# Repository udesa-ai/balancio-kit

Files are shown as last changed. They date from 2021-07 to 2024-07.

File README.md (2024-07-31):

# Balancio-Kit


&nbsp;

&nbsp;



#### [README in English](README_EN.md)
----
Proyecto educativo de un robot :robot: de autobalanceo de ultra bajo costo, capaz de correr una red neuronal para mantener el equilibrio y de ser controlado de manera inalámbrica  :trackball:.

Desarrollado con fines didácticos para enseñar conceptos de RL, ML, AI y control.

<p align="center">
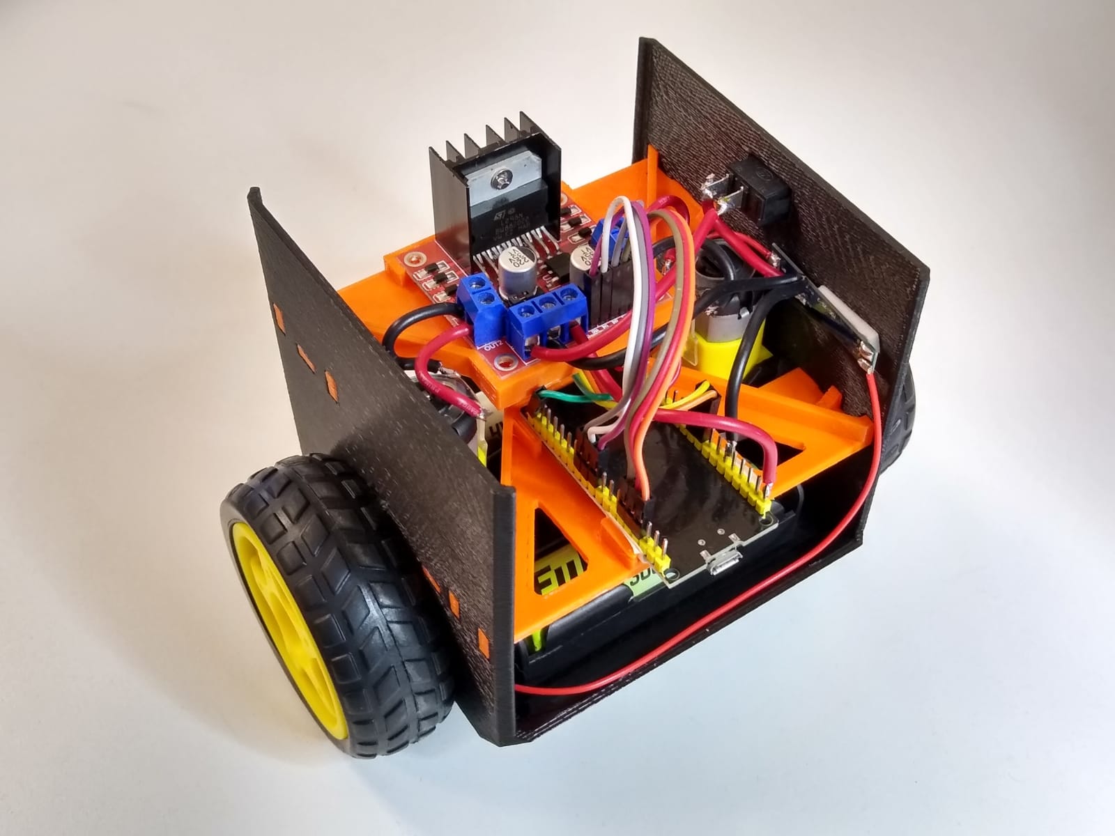
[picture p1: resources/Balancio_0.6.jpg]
    
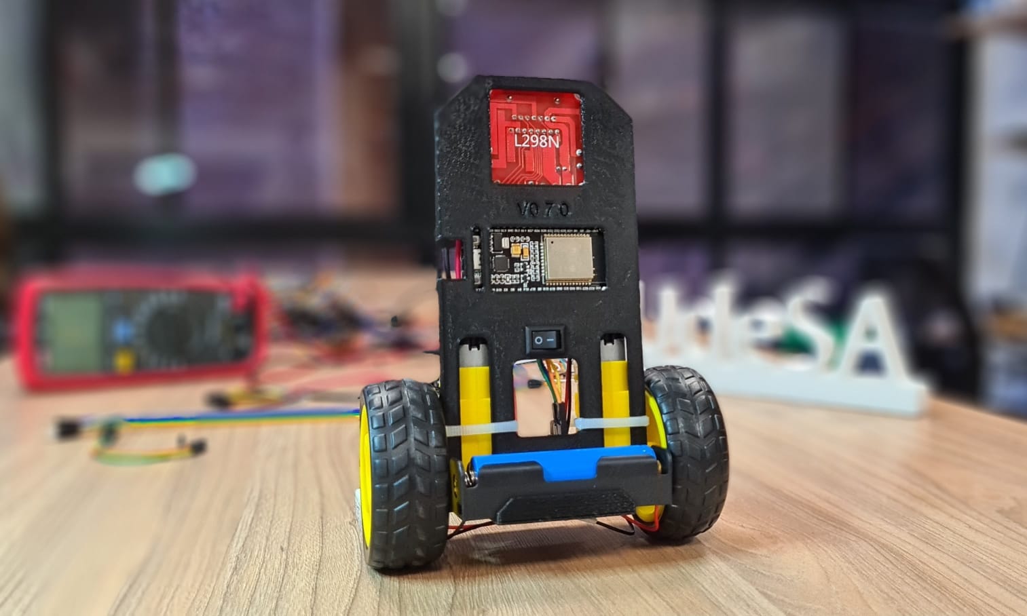
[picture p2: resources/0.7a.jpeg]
    
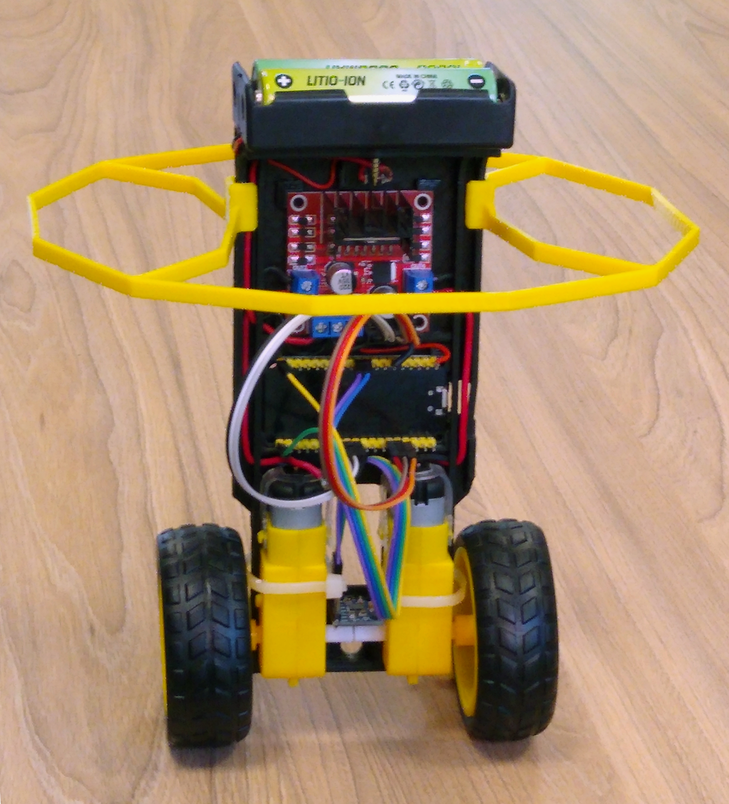
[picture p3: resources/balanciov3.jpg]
    
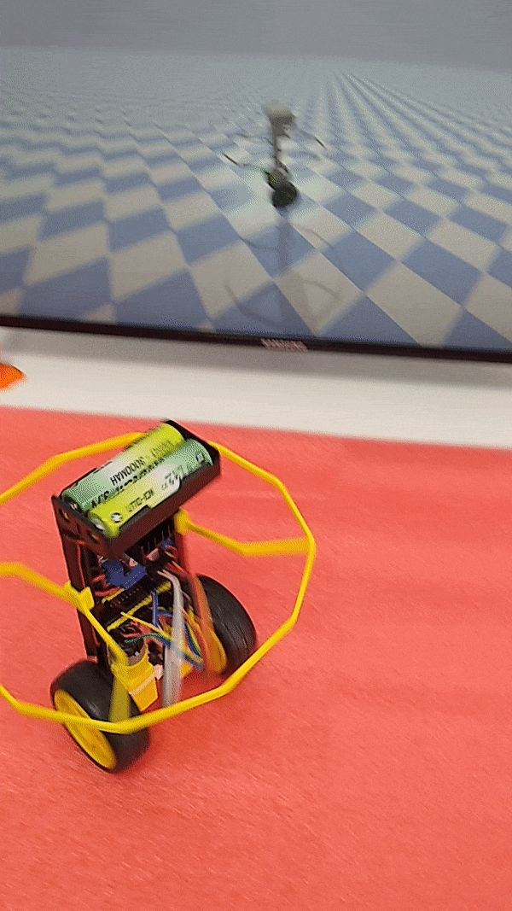
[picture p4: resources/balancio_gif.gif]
    
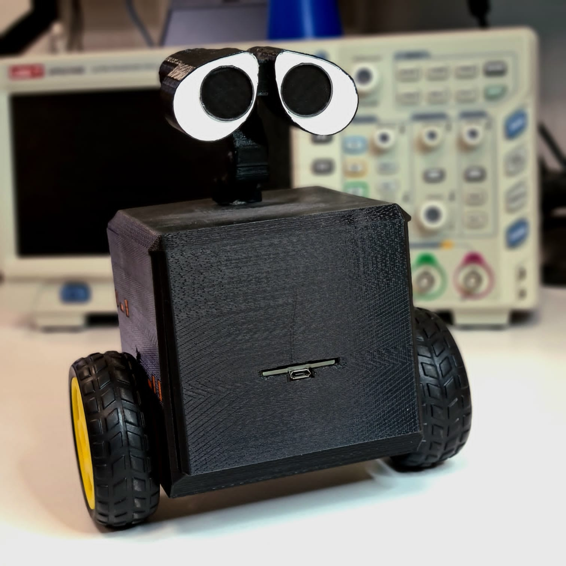
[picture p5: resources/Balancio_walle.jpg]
    
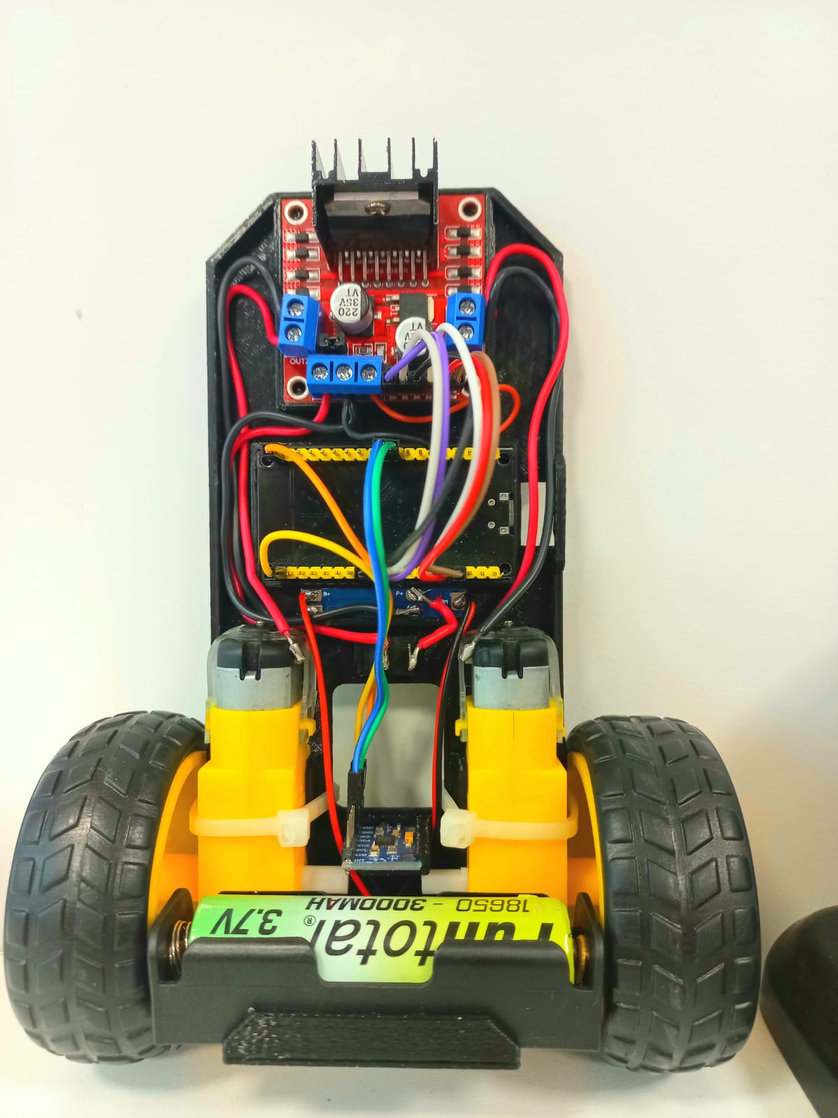
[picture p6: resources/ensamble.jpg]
    
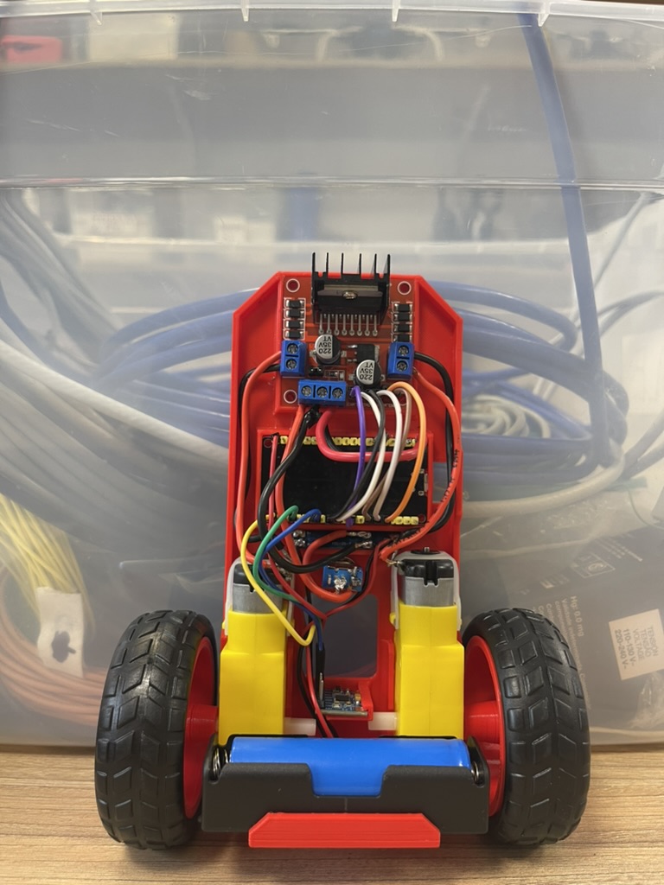
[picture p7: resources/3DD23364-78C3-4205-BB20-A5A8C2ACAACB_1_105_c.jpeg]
    
</p>

## Versiones
| | Estabilidad | Facilidad de Armado  | Requiere I3D | Tiempo de [I3D](#configuración-de-impresión)| Plano de Impresión 3D| Foto de la versión |
|:---:|:---:|:---:|---|:---:|:---:|:---:|
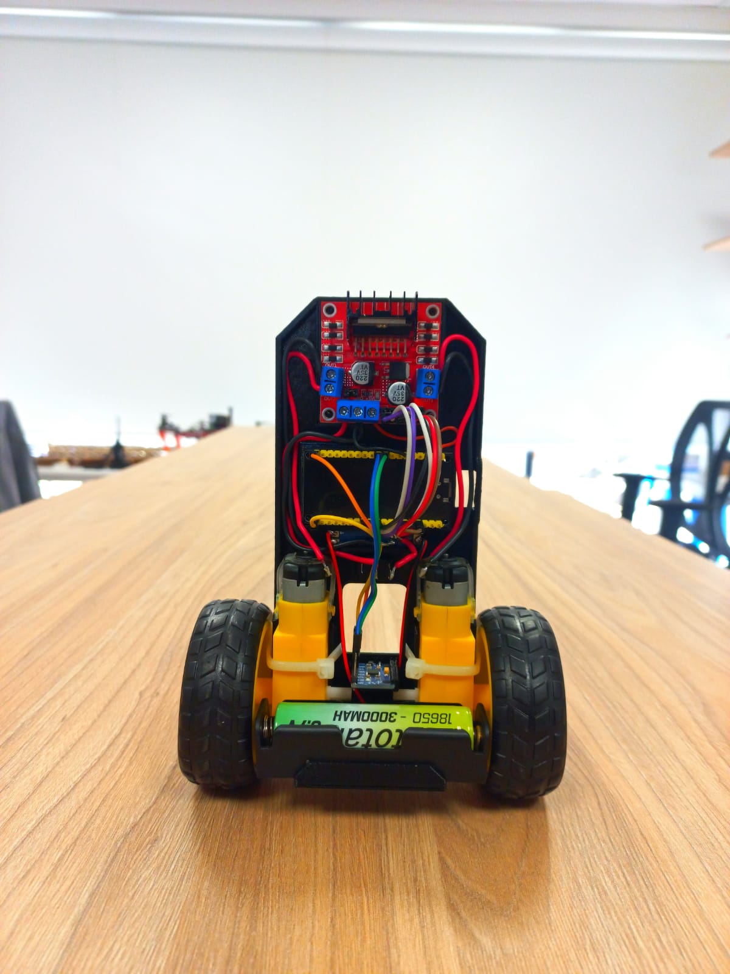
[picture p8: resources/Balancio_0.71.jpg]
| V 0.7 (Recomendado) | :star: :star: :star: | :star: :star: :star: | SI | <ul style="list-style-type:none;"> <li>  Baterias 47m </li> <li> Cuerpo 2:36 h </li> </ul> | <A HREF="https://github.com/AaronLoz/balancio-kit/tree/RL_1/Planos%20de%20Impresi%C3%B3n%203D/Version%200.7"> Versión 0.7 I3D</A> |  |
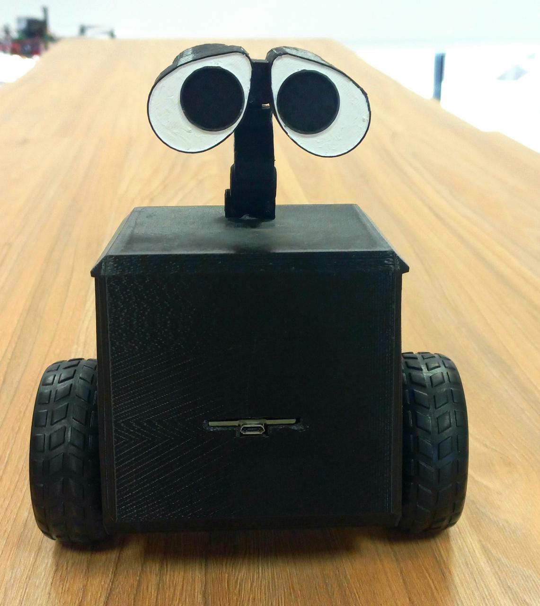
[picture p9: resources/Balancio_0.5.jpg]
| V 0.6 AKA:Wall-e | :star: :star: :star: | :star: | SI | <ul style="list-style-type:none;"> <li> C_Inferior 5:25h </li> <li> C_Superior 5:11h </li> <li>P_inferior 58m</li> <li>P_superior 55m</li> <li> Cabeza 3:19 h </li> </ul> | <A HREF="https://github.com/AaronLoz/balancio-kit/tree/RL_1/Planos%20de%20Impresi%C3%B3n%203D/Versi%C3%B3n%200.6"> Versión 0.6 I3D</A> |   |
| V 0.5 | :star: | :star: :star: :star: | SI |<ul> <li>Aro 49m </li> <li> Cuerpo 4:42h </li> | <A HREF="https://github.com/AaronLoz/balancio-kit/tree/RL_1/Planos%20de%20Impresi%C3%B3n%203D/versi%C3%B3n%200.5"> Versión 0.5 I3D</A> |  |
    
### Configuración de Impresión 
- Espesor de boquilla: 0.4 mm
- Altura de Capa: 0.3 mm 
- Perimetros: 3 
- Capas Solidas Top y Bottom:  3 
- Infill: 20%

## Componentes
| Componente | Imagen del Componente |
|:---:|:---:|
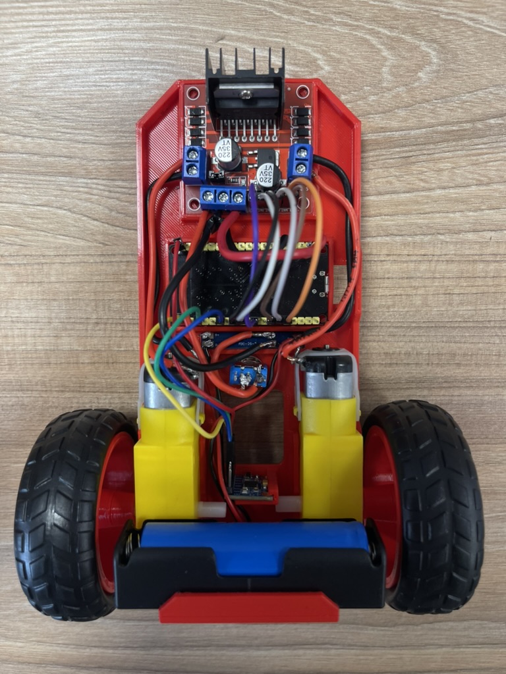
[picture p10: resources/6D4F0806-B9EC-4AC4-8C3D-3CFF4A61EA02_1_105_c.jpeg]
| Placa base (estructura en impresion 3D) |  |
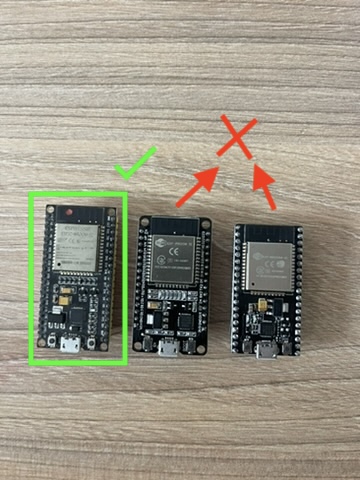
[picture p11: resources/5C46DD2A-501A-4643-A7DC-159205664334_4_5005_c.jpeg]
| Microcontrolador NodeMCU ESP32 |  |
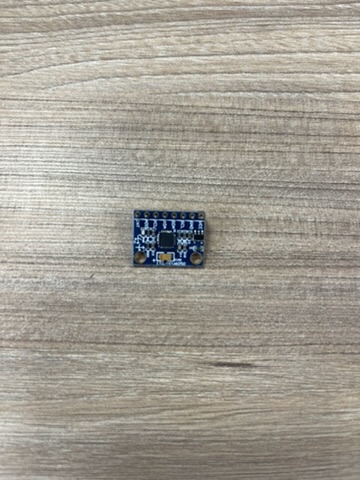
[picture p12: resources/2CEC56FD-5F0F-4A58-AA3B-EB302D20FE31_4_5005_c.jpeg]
| IMU MPU 6050 |  |
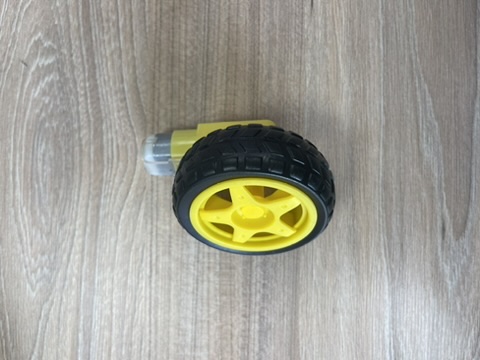
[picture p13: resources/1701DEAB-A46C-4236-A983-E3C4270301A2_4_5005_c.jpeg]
| 2 motorreductores de 6v con rueda "para Arduino" |  |
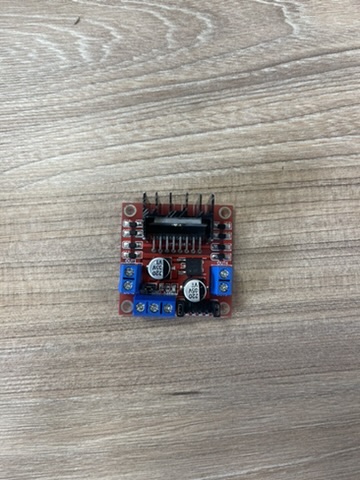
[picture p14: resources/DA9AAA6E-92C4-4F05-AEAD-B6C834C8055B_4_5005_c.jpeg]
| Puente-H L298N |  |
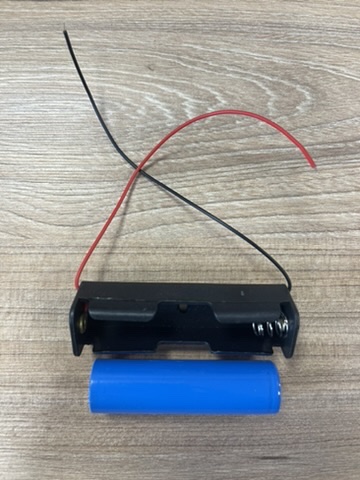
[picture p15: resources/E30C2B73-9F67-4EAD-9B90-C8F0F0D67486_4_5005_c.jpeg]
| 2 baterías 18650 con su correspondiente porta-pilas |  |
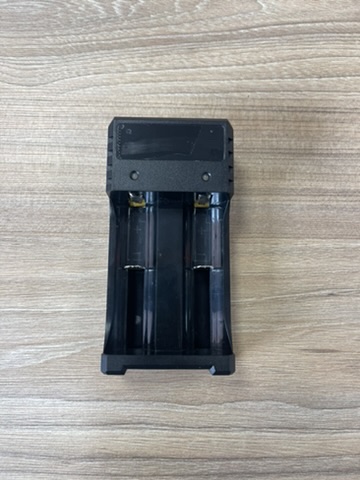
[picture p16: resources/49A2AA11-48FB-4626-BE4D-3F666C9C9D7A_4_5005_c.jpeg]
| Cargador de baterias doble |  |
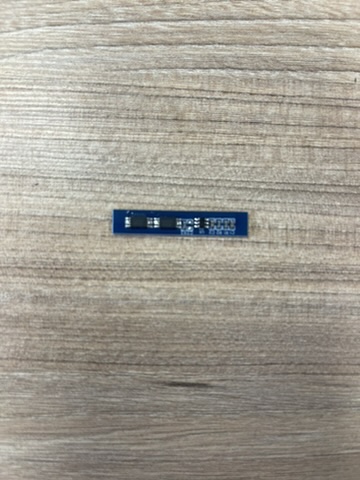
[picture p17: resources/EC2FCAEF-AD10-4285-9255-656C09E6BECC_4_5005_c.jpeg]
| BMS FCD-2S-2 |  |
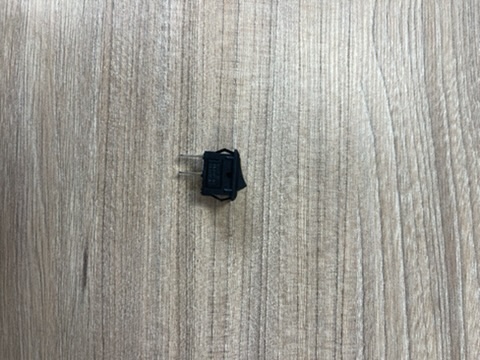
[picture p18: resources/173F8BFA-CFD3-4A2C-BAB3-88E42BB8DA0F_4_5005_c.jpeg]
| Switch |  |
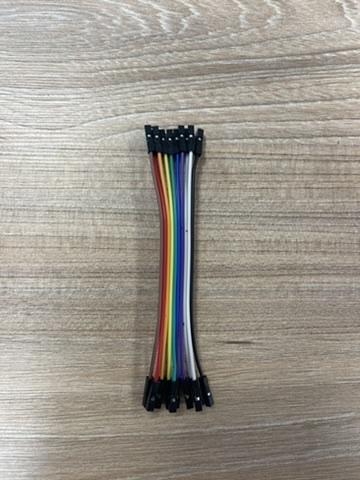
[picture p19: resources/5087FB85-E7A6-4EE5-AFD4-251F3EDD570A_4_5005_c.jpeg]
| 10 Cables DuPont |  |
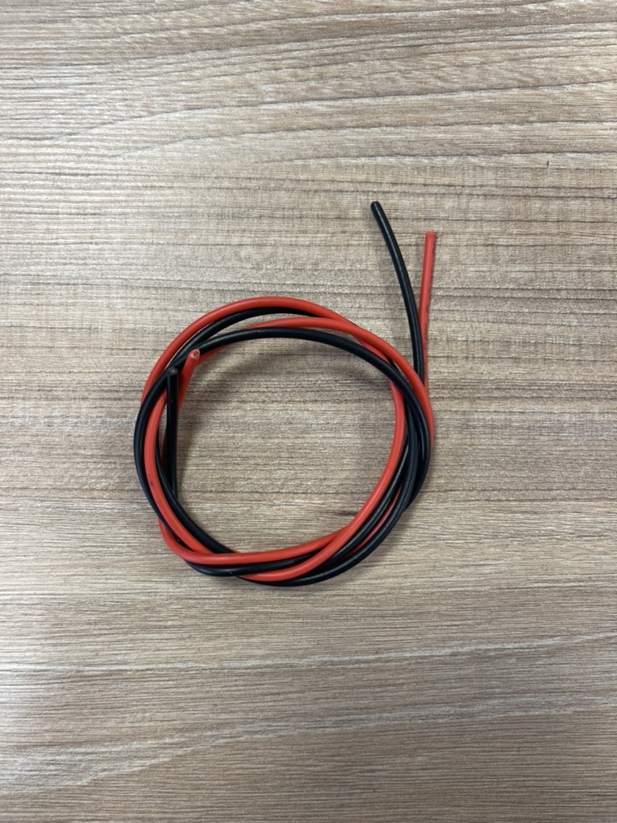
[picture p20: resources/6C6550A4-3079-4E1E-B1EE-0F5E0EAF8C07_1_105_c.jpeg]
| 1m Cable eléctrico unipolar (2x50 cm. c/u) |  |

<p align="center">
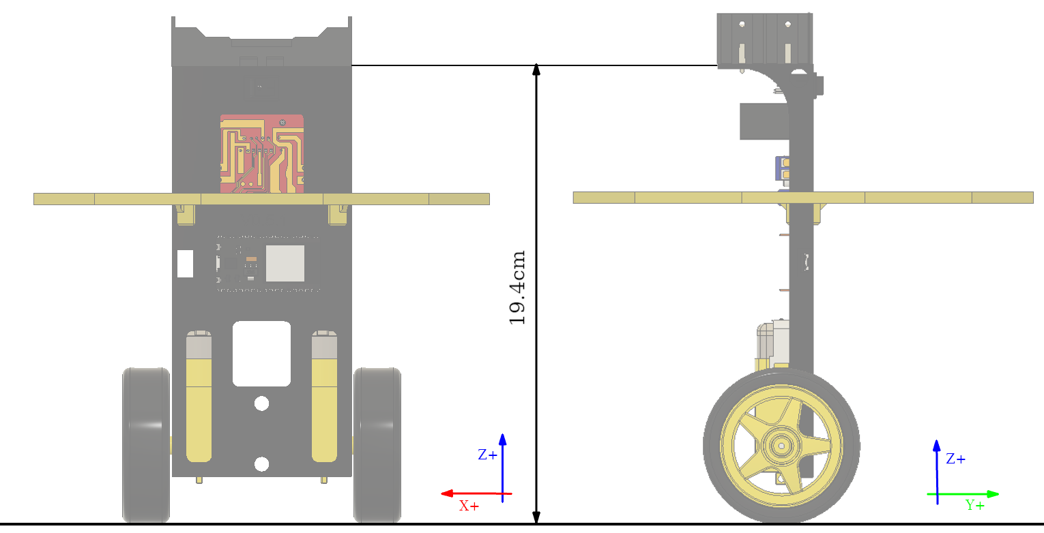
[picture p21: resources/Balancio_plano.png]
    
</p>

## Plano Electrico 
<p align="center">
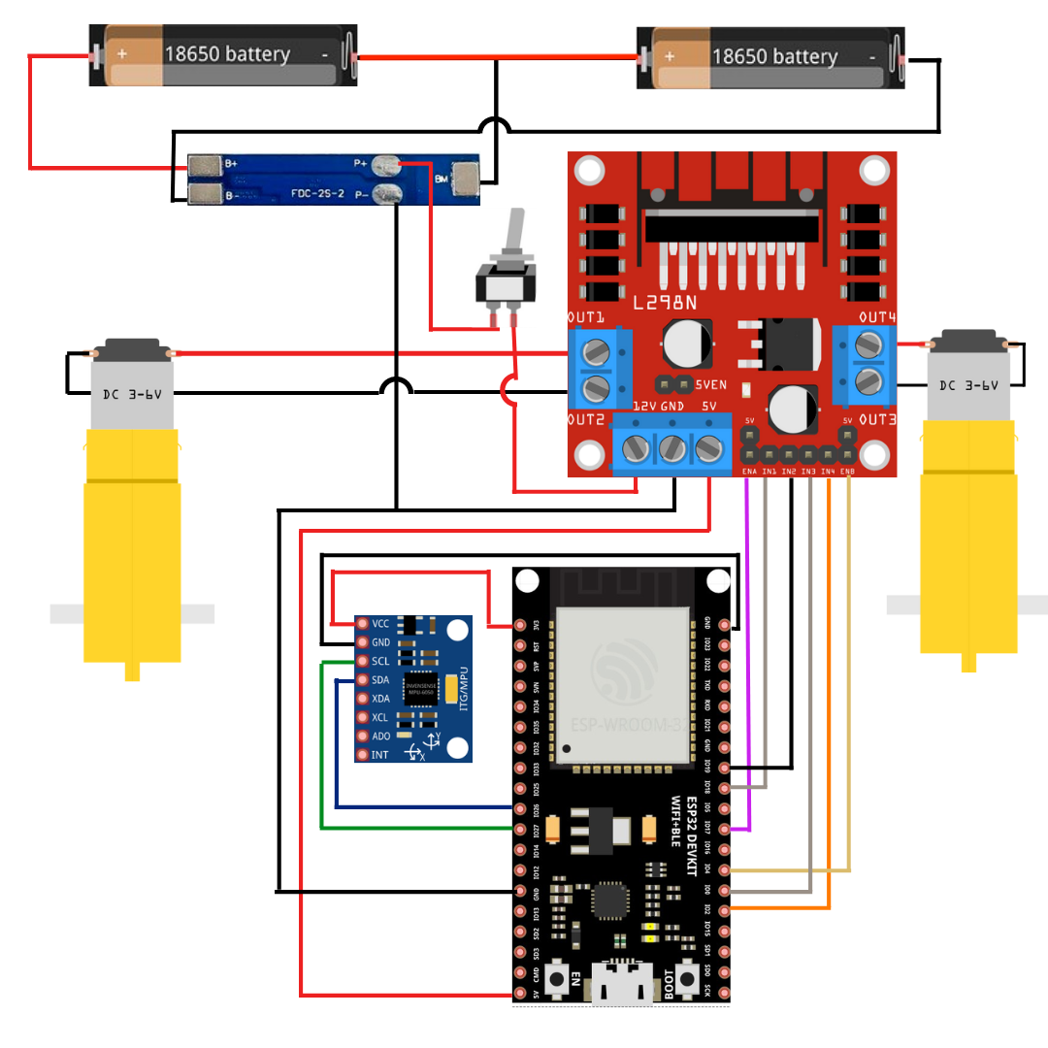
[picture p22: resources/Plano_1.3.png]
    
</p>    
    
## Ensamblaje Mecánico 
1. Imprimir en 3D alguna de las [versiones](#versiones).
1. Encastrar piezas en su posición final.
1. Sostener los motores con precintos y/o pegamento. 
1. Conectar los componentes siguiendo el [plano electrico](#plano-electrico).  
     
## Instalación :floppy_disk:

En primer lugar, se debe clonar el repositorio. Esto se puede realizar tanto descargando el mismo
como un .ZIP, o ejecutando `git clone https://github.com/UDESA-AI/balancio-kit.git` en consola.

La instalación consta de 3 módulos principales: Microcontrolador, simulación y aplicación.
Éstos son fundamentales para el funcionamiento completo del proyecto, pero la instalación
de cada uno de ellos se puede realizar en distinto orden.

### Microcontrolador

<details open>
<summary>Instalación de la IDE</summary> 
Para programar y compilar el NodeMCU ESP32 usaremos la IDE 2 de Arduino. Para esto se
debe instalar la misma siguiendo los pasos que se especifican en el siguiente 
[link](https://www.arduino.cc/en/software) .
</details> 
<details open>
<summary>Configuración del Microcrontolador</summary> 
Una vez instalada la IDE, se debe habilitar el microcontrolador que vamos a usar.
Para esto se deben seguir los siguientes pasos:
    
1. En la IDE, ir a 'File' (Archivos) → 'Preferences' (Preferencias)
    
2. En el campo "Additional Boards Manager URLs", agregar lo siguiente: https://dl.espressif.com/dl/package_esp32_index.json. (Luego clickear 'OK').
3. Ir a 'Tools' → 'Board: ' → 'Boards Manager…' 
    
4. Buscar "esp32", e instalar "esp32 by Espressif Systems" (version 2.x) presionando el botón 'Install'.
    
5. Indicarle a la IDE que vamos a utilizar un esp32. Ir a 'Tools' → 'Board:' → 'ESP32 Arduino' → 'NodeMCU-32S'
    
6. En 'Tools' → 'Port', seleccionar el puerto correspondiente a donde está conectado el microcontrolador.

</details> 

<details open>
<summary>Librerias de Arduino</summary> 
Luego procederemos a instalar las librerías de arduino que vamos a utilizar:

- Para eso ir a 'Sketch' → 'Include Library' → 'Manage Libraries…'

- Buscar e instalar las siguientes librerias, especificando la versión correspondiente:
    - MPU6050 by Electronic Cats (version 1.0.0)
    - PS3 Controller Host by Jeffrey van Pernis (version 1.1.0)
    - EloquentTinyML by Simone Salerno (version 0.0.7)

</details> 
<details open>
<summary>Ejecución inicial</summary> 
Para comprobar la instalación, ejecutaremos un ejemplo de prueba:
- ir a 'File' → 'Examples' → 'WiFi' → 'WiFiScan'
- En el sketch generado, presionar el botón de carga ('Upload')  :calling:
- Si todo funcionó correctamente, debe aparecer un mensaje 'Done uploading' en la consola.

Posibles errores:
- Si no se puede cargar el programa al microcontrolador, intentar mantener presionado el botón "boot" presente en la placa, mientras se realiza la carga. Esto se debería realizar solo la primera vez.
</details> 

### Simulación
La simulación es opcional, no es necesaria para el funcionamiento y armado del robot. Se puede pasar directamente a la parte de calibración.
<details open>
 
La simulación corre en Python :snake:, y utiliza diversos paquetes. Para facilitar la instalación de los mismos, utilizaremos [Conda](https://docs.conda.io/en/latest/).

Se debe seguir con los siguientes pasos:

1. Para el uso e instalación de conda, descargaremos miniconda (también se puede instalar [Anaconda](https://docs.anaconda.com/anaconda/install/index.html)), siguiendo con los pasos que se especifican en el siguiente [link](https://docs.conda.io/en/latest/miniconda.html#installing).
2. Crearemos un 'Environment' de conda, donde alojaremos nuestros paquetes. 
   Esto se puede realizar tanto desde la consola (en el caso de haber descargado Miniconda) o desde una GUI (en caso de haber descargado Anaconda). Respectivamente:
    - Miniconda: Ejecutar el siguiente comando en la consola: `conda env create -f requirements.yml`. Donde `requierments.yml` es el [archivo](https://github.com/UDESA-AI/balancio-kit/blob/RL_1/requirements.yml) que se encuentra dentro del repositorio y ya fue descargado.
    - Anaconda: En la GUI de Anaconda: En la pestaña environments, hacer clik en import y especificar [archivo](https://github.com/UDESA-AI/balancio-kit/blob/RL_1/requirements.yml) en file

<p align="center">
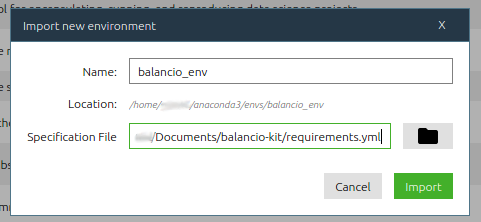
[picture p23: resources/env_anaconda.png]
    
</p>

3. Activar el environment creado, llamado **balancio**:
    - Miniconda: Ejecutar en terminal `conda activate balancio`
    - Anaconda: En la pestaña environments, hacer clik en el ambiente que se quiere activar
4. Dentro del environment activado, ejecutar el archivo [setup.py](https://github.com/UDESA-AI/balancio-kit/blob/RL_1/simulation/balancio_lib/setup.py):
    `python setup.py`
5. Probar la instalación, corriendo el siguiente [script](https://github.com/UDESA-AI/balancio-kit/blob/RL_1/simulation/pid.py):
    `python pid.py`
    </details> 

### Variables Físicas de la versión 0.7
#### Cuerpo
Masa sin ruedas: 0.244 kg

Posición del centro de masa con respecto al eje de los motores y el centro simétrico del cuerpo: 

- x = 1.55 
- y ~= 0 mm
- z = 31 mm

Inercia sin ruedas desde el centro de masa (kg.m2): 

- Ixx = 0.0006945
- Ixy ~= 0
- Iyy = 0.0006536
- Ixz = -0.000013447 
- Iyz ~= 0
- Izz = 0.0001937

#### Rueda
Masa de una rueda: 0.029 kg

Posición del centro de masa con respecto al eje de los motores y el borde del agarre: 
- x = 0 mm   
- y = 15.6 mm 
- z = 0 mm

Inercia de la rueda desde el centro de masa (kg.m2):  

- Ixx = 0.000011729 
- Ixy ~= 0  
- Iyy = 0.000021531 
- Ixz ~= 0 
- Iyz ~= 0 
- Izz = 0.000011729

### Aplicación 

 La aplicación está creada en <A HREF="https://appinventor.mit.edu/"> MIT App Inventor </A>.

Simplemente entrar al website e importar el .aia en <A HREF="Balancio-kit/app/app.aia"> App Balancio  </A>. Luego de esto, se puede usar la aplicación mediante bluethooth desde un celular.

## Calibración

Estas instrucciones asumen conocimiento del uso de la IDE arduino

<details open>
<summary>Calibración del IMU</summary>
1. Abrir `Balancio-kit/Mcu/Src/imu_calibration/imu_calibration.ino` con el IDE Arduino
    
2. Colocar el robot con la IMU paralela al piso y mantenerlo firme

3. Subir el programa a la placa y usar el monitor serial para obtener las compensaciones de la IMU

4. Modificar las compensaciones de giróscopo en el archivo `balancio-kit/mcu/src/main/config.h` en:
```c++
// IMU calibration parameters
#define X_ACCEL_OFFSET -1775
#define Y_ACCEL_OFFSET  756
#define Z_ACCEL_OFFSET  2706
#define X_GYRO_OFFSET   181
#define Y_GYRO_OFFSET   77
#define Z_GYRO_OFFSET   60
```
5. Para las compensaciones de Acelerómetro debe ser tenido en cuenta la gravedad, solo midiendo las compensaciones con la gravedad perpendicualar a esa direcci 
</details>  

<details open>
<summary>Calibración del angulo de equilibrio</summary>
1. Abrir `balancio-kit/mcu/src/main/main.ino`

2. Sostener el robot en la posición de equilibrio

3. Subir el programa a la placa y usar el monitor serial para obtener las compensaciones de angulo

4. Modificar en angulo de equilibrio en el archivo `balancio-kit/mcu/src/main/config.h` en la línea:
```c++
// Angle of (approximate) static equilibrium
#define STATIC_ANGLE -0.04 // Calibrated point
```
 </details>   
 
<details open>
<summary>Calibración de las constantes PID</summary>
    
1. Sacar el jumper de 12v en el driver 

2. Elegir parámetros PID
    
3. modificar las constantes del PID en el archivo `balancio-kit/mcu/src/main/config.h` en las líneas:
```c++
// PID Constants for pitch control
#define KP 2000
#define KI 22000
#define KD 20.0
```   

4. Probar las constantes, si se sacó el jumper se puede probar incluso con el cable conectado. **Cuidado al hacer esto!**

---
</details> 
     
Una vez configurado correctamente el robot, se pueden seleccionar distintos parametros de configuracion en el archivo correspondiente (`config.h`). 

Entre ellos, se puede seleccionar el tipo de controlador deseado para estabilizar el Balancio.

Por ejemplo, en caso de querer utilizar un controlador PID:
```c++
// Control algorithm type
#define CONTROL_ALGO "PID"
```

En caso de querer utilzar un agente de aprendizaje por refuerzo:
```c++
// Control algorithm type
#define CONTROL_ALGO "RL"
```
</details> 

---
## TODO

- [x] initial commit
- [x] Desarrollar aplicación bluetooth
- [x] Crear agente RL
- [x] Diseño mecánico
- [X] Publicar STL del diseño mecánico
- [ ] Publicar STEP del diseño mecánico
- [X] Crear diagrama electrónico
- [ ] Aclarar que datos levantar del imu calibration.

## Bugs conocidos
- [x] Wheel spins on startup

## Contribuciones
 
Las *pull requests* son bienvenidas, para cambios mayores, por favor abrir un *issue* para discutir los cambios deseados

## Licencia
[MIT](https://choosealicense.com/licenses/mit/)

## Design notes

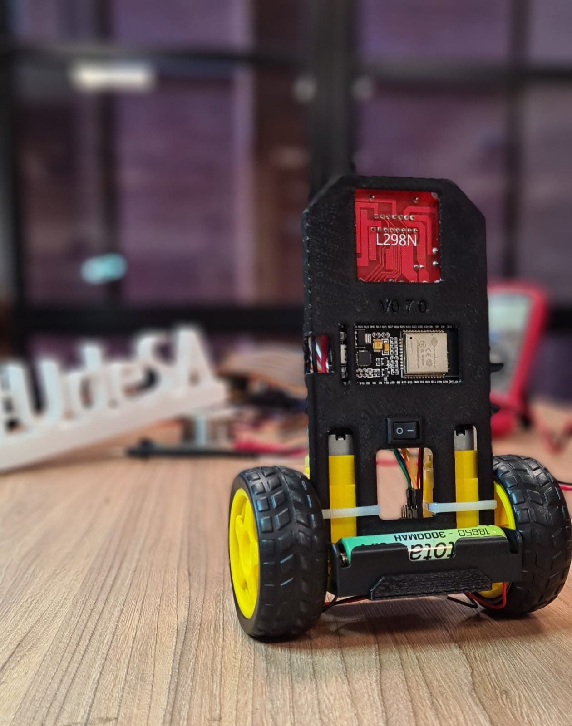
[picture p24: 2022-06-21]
resources/0.7b.jpeg

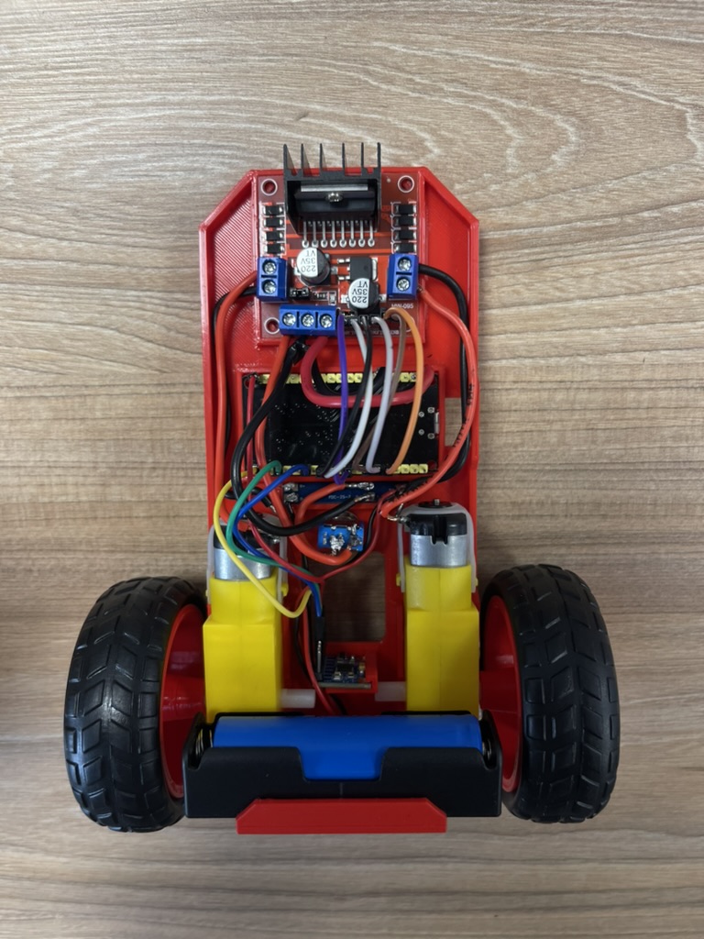
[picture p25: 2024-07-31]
resources/710C4956-F81B-4884-B3D5-5948F854DA13_1_105_c.jpeg

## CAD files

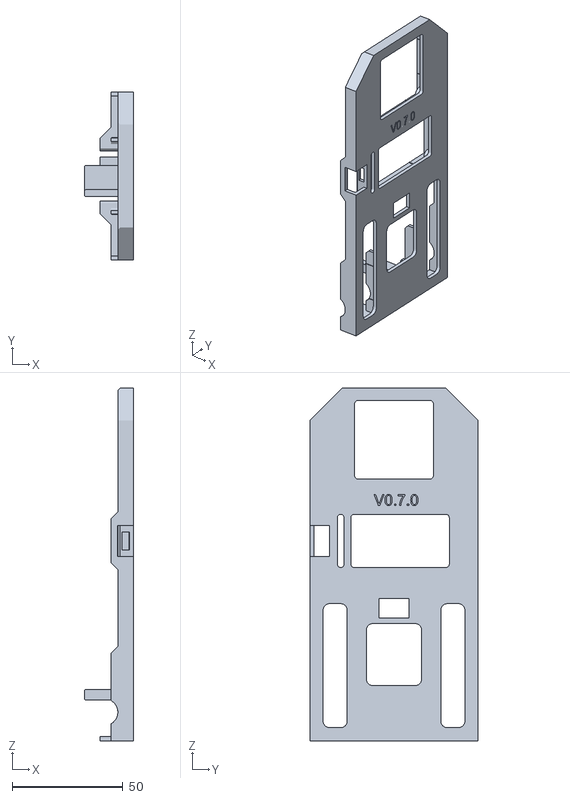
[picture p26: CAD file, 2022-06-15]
Planos de Impresión 3D/Version 0.7/Body_v0.7.stl
22.0 x 76.0 x 159.3

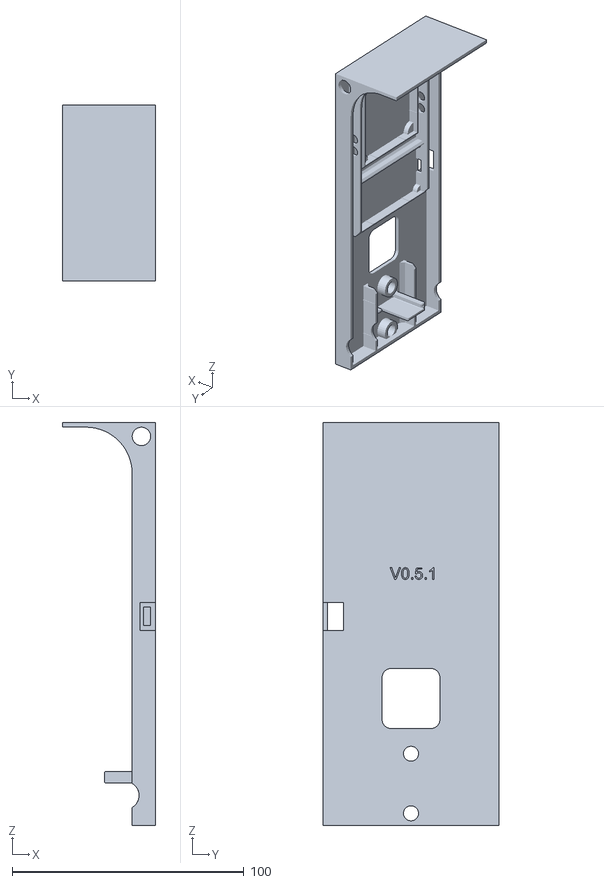
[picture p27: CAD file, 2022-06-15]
Planos de Impresión 3D/versión 0.5/Cuerpo.stl
40.0 x 76.0 x 174.0

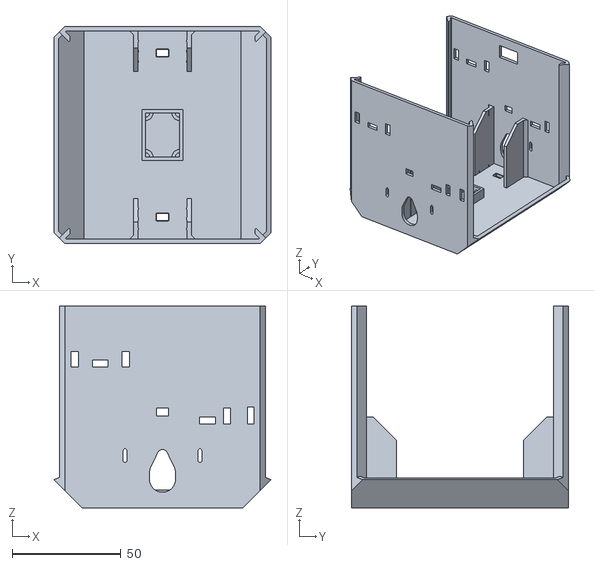
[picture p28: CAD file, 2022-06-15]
Planos de Impresión 3D/Versión 0.6/Cuerpo_Inferior.stl
100.0 x 100.0 x 93.0

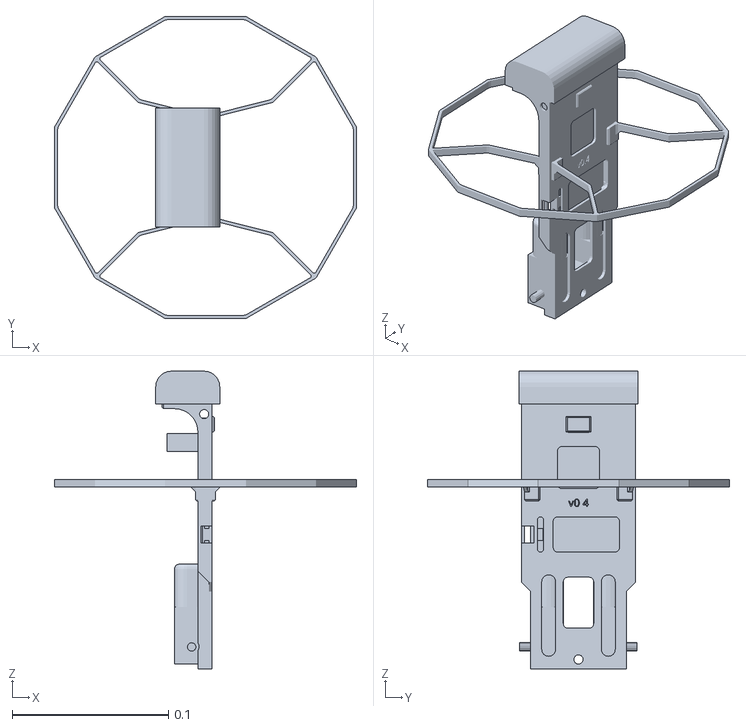
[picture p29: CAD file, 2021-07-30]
simulation/stl/Body.stl
0.193 x 0.193 x 0.19

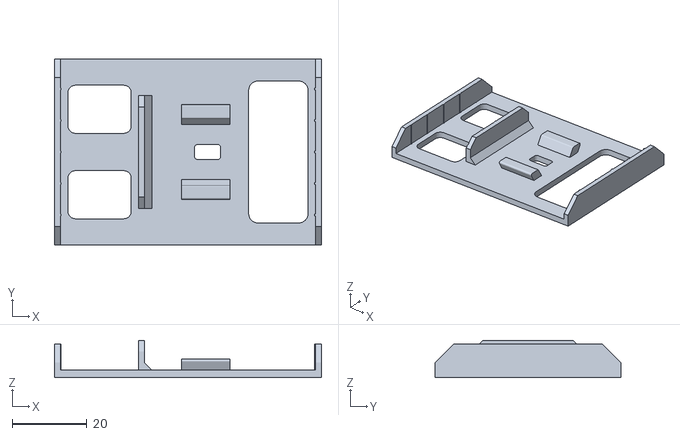
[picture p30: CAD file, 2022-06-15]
Planos de Impresión 3D/Version 0.7/Battery_Holder_Holder.stl
71.5 x 49.8 x 10.0

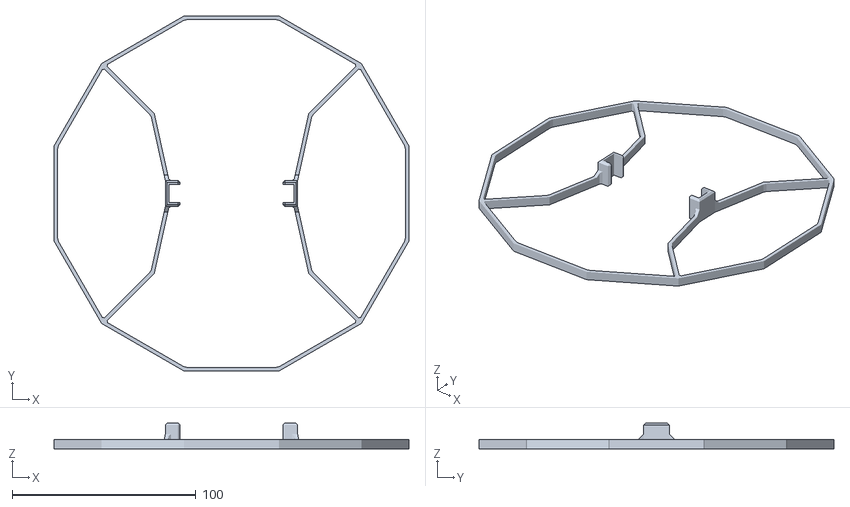
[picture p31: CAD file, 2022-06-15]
Planos de Impresión 3D/versión 0.5/Bumper.stl
193.2 x 193.2 x 14.0

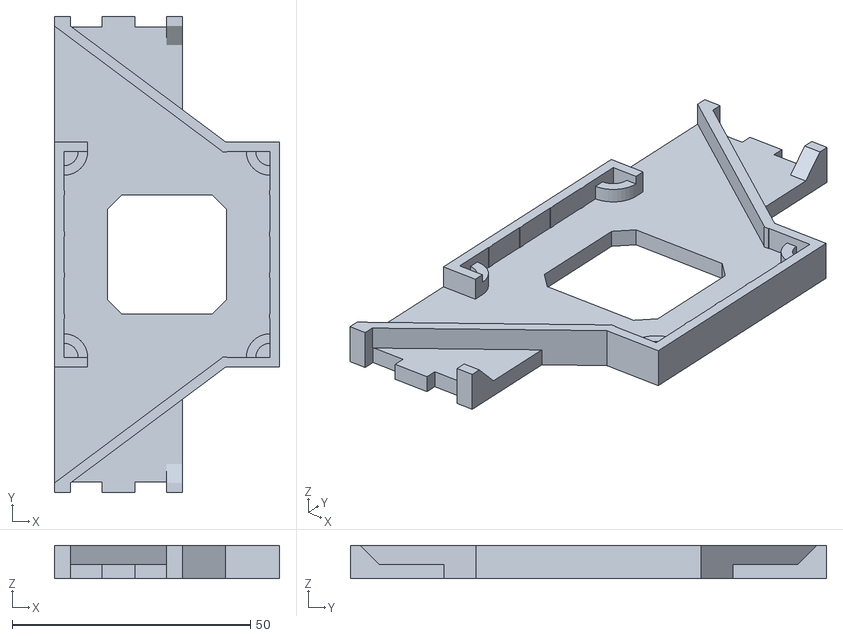
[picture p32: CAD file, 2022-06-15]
Planos de Impresión 3D/Versión 0.6/Placa_Superior.stl
47.3 x 100.0 x 7.00

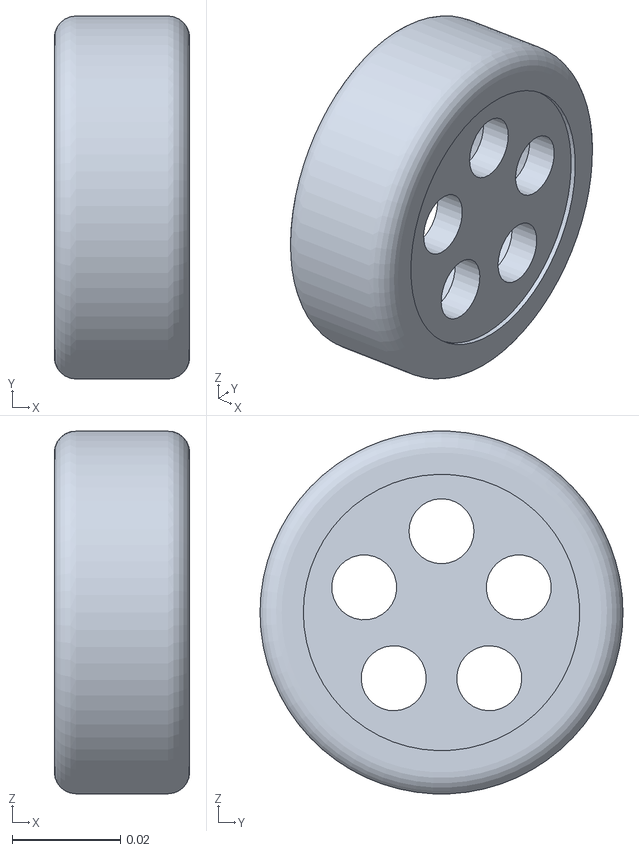
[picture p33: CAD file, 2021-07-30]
simulation/stl/Wheel.stl
0.025 x 0.067 x 0.0669

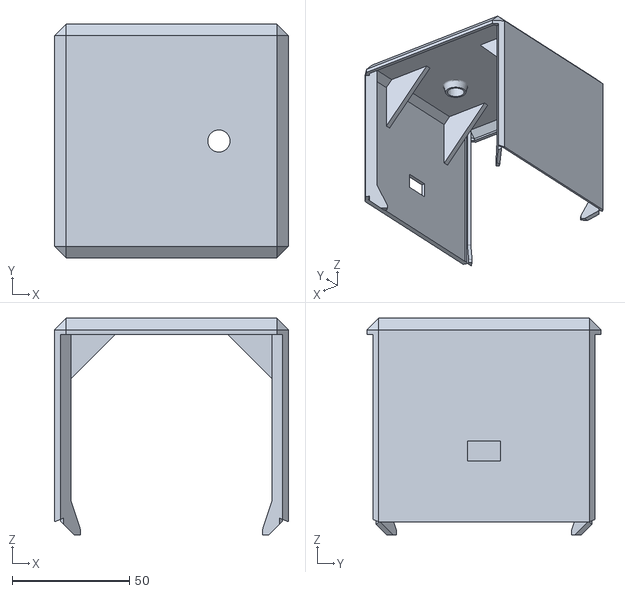
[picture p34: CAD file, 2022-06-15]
Planos de Impresión 3D/Versión 0.6/Cuerpo_Superior.stl
100.0 x 100.0 x 92.5

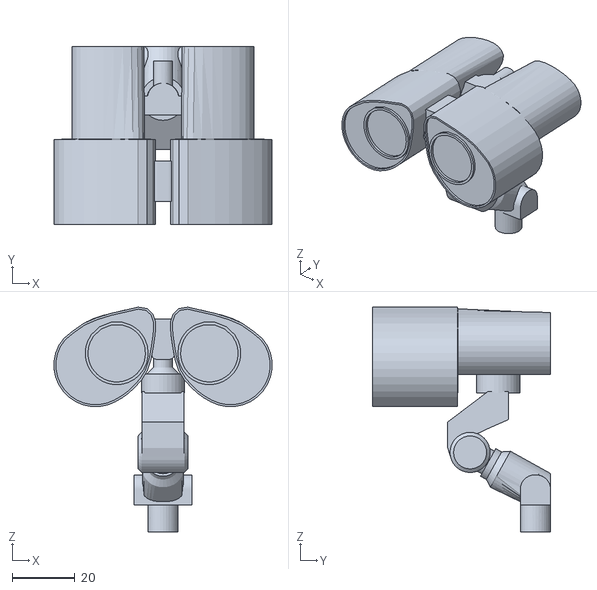
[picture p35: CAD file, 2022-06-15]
Planos de Impresión 3D/Versión 0.6/walle_ojos.stl
69.3 x 56.6 x 71.4

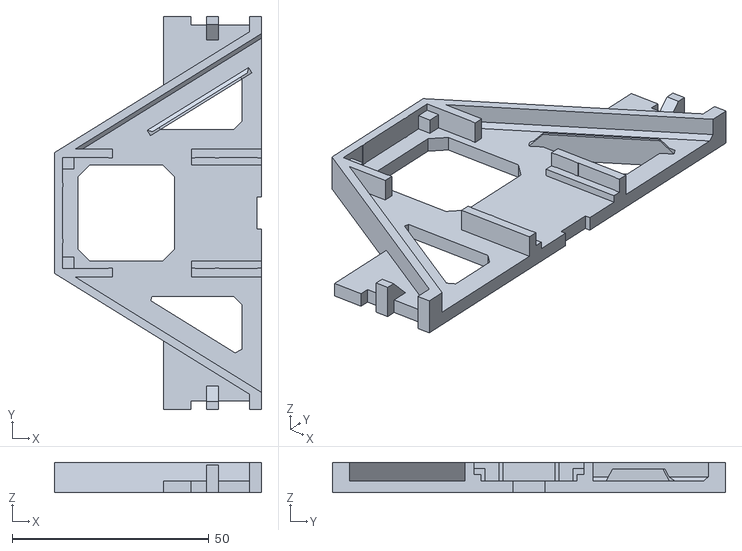
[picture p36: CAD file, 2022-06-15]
Planos de Impresión 3D/Versión 0.6/Placa_Inferior.stl
52.7 x 100.0 x 7.67

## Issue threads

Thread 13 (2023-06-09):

Cambios readme

AlexBodner, 2023-06-09:
- Cambiar simulacion por calibración
- Sacar lo de probar el modulo de wifi

AlexBodner, 2023-06-09:
- Tambien se podría sumar en la calibracion una aclaracion de que los valores que hay que tomar son los de la última linea que dice //OFFSETS

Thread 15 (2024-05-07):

Add battery preotector explanation to README

Gabo-Tor, 2024-05-07:
si se cambia la batería hay que puentear B-  y P- para resetear el protector e batería en algunos modelos

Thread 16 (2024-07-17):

Update from esp32 lib 2.x to 3.x

Gabo-Tor, 2024-07-17:
There have been breaking changes from 2 to 3
https://docs.espressif.com/projects/arduino-esp32/en/latest/migration_guides/2.x_to_3.0.html

Gabo-Tor, 2024-07-31:
fixed

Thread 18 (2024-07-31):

fix switch image in blueprint

Gabo-Tor, 2024-07-31:

Gabo-Tor, 2024-09-16:
the switch shown is not the one used in the robot

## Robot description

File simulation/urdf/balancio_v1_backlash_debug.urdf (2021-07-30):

<?xml version="1.0" ?>
<robot name="balancio" xmlns:xacro="http://www.ros.org/wiki/xacro">

  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

  <link name="link_chassis">
    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
    <pose>0 0 0 0 0 0</pose>
    <inertial>
      <mass value="0.5"/>
      <origin rpy="0 0 0" xyz="0 0 0"/>
      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
    </inertial>
    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
  </link>


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

  <joint name="joint_left_gb" type="continuous">  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
    <origin rpy="0 0 0" xyz="0 0.17 -0.3"/>
    <child link="link_left_gb"/>
    <parent link="link_chassis"/>
    <axis rpy="0 0 0" xyz="0 1 0"/>
    <limit effort="0.8" velocity="30"/>
    <dynamics damping="0.0005" friction="0.0005"/>  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
    <safety_controller k_velocity="0.026"/>  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
  </joint>

  <link name="link_left_gb">
    <inertial>
      <mass value="0.1"/>
      <origin rpy="0 1.5707 1.5707" xyz="0 0 0"/>
      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
    </inertial>
    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
  </link>

  <joint name="joint_left_wheel" type="revolute">  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
    <limit lower="-0.2" upper="0.2" />
    <origin rpy="0 0 0" xyz="0 0.04 0"/>
    <child link="link_left_wheel"/>
    <parent link="link_left_gb"/>
    <axis rpy="0 0 0" xyz="0 1 0"/>
    <limit effort="0.8" velocity="30"/>
    <dynamics damping="0.0005" friction="0.0005"/>  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
    <safety_controller k_velocity="0.026"/>  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
  </joint>

  <link name="link_left_wheel">
    <inertial>
      <mass value="0.1"/>
      <origin rpy="0 1.5707 1.5707" xyz="0 0 0"/>
      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
    </inertial>
    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
  </link>


  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
  <joint name="joint_left_gb_marker" type="fixed">  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
    <origin rpy="0 0 0" xyz="0 0 0.05"/>
    <child link="link_left_gb_marker"/>
    <parent link="link_left_gb"/>
    <axis rpy="0 0 0" xyz="0 1 0"/>
  </joint>

  <link name="link_left_gb_marker">
    <inertial>
      <mass value="0.001"/>
      <origin rpy="0 1.5707 1.5707" xyz="0 0 0"/>
      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
    </inertial>
    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
  </link>

  <joint name="joint_left_wheel_marker" type="fixed">  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
    <origin rpy="0 0 0" xyz="0 0 0.1"/>
    <child link="link_left_wheel_marker"/>
    <parent link="link_left_wheel"/>
    <axis rpy="0 0 0" xyz="0 1 0"/>
  </joint>

  <link name="link_left_wheel_marker">
    <inertial>
      <mass value="0.001"/>
      <origin rpy="0 1.5707 1.5707" xyz="0 0 0"/>
      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
    </inertial>
    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
  </link>

  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

  <joint name="joint_right_gb" type="continuous">  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
    <origin rpy="0 0 0" xyz="0 -0.17 -0.3"/>
    <child link="link_right_gb"/>
    <parent link="link_chassis"/>
    <axis rpy="0 0 0" xyz="0 1 0"/>
    <limit effort="0.8" velocity="30"/>
    <dynamics damping="0.0005" friction="0.0005"/>  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
    <safety_controller k_velocity="0.026"/>  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
  </joint>

  <link name="link_right_gb">
    <inertial>
      <mass value="0.1"/>
      <origin rpy="0 1.5707 1.5707" xyz="0 0 0"/>
      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
    </inertial>
    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
  </link>

  <joint name="joint_right_wheel" type="revolute">  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
    <limit lower="-0.2" upper="0.2" />
    <origin rpy="0 0 0" xyz="0 -0.04 0"/>
    <child link="link_right_wheel"/>
    <parent link="link_right_gb"/>
    <axis rpy="0 0 0" xyz="0 1 0"/>
		<limit effort="0.8" velocity="30"/>
    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
  	<dynamics damping="0.0005" friction="0.0005"/>  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
		<safety_controller k_velocity="0.026"/>  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
  </joint>

  <link name="link_right_wheel">
    <inertial>
      <mass value="0.1"/>
      <origin rpy="0 1.5707 1.5707" xyz="0 0 0"/>
      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
    </inertial>
    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
  </link>

  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
  <joint name="joint_right_gb_marker" type="fixed">  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
    <origin rpy="0 0 0" xyz="0 0 0.05"/>
    <child link="link_right_gb_marker"/>
    <parent link="link_right_gb"/>
    <axis rpy="0 0 0" xyz="0 1 0"/>
  </joint>

  <link name="link_right_gb_marker">
    <inertial>
      <mass value="0.001"/>
      <origin rpy="0 1.5707 1.5707" xyz="0 0 0"/>
      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
    </inertial>
    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
  </link>

  <joint name="joint_right_wheel_marker" type="fixed">  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
    <origin rpy="0 0 0" xyz="0 0 0.1"/>
    <child link="link_right_wheel_marker"/>
    <parent link="link_right_wheel"/>
    <axis rpy="0 0 0" xyz="0 1 0"/>
  </joint>

  <link name="link_right_wheel_marker">
    <inertial>
      <mass value="0.001"/>
      <origin rpy="0 1.5707 1.5707" xyz="0 0 0"/>
      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
    </inertial>
    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
  </link>

  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

</robot>

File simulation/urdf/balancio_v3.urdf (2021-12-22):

<?xml version="1.0" ?>
<robot name="balancio" xmlns:xacro="http://www.ros.org/wiki/xacro">

  <material name="black">
    <color rgba="0.0 0.0 0.0 0.8"/>
  </material>
  <material name="blue">
    <color rgba="0.203125 0.23828125 0.28515625 0.8"/>
  </material>
  <material name="green">
    <color rgba="0.0 0.8 0.0 0.8"/>
  </material>
  <material name="grey">
    <color rgba="0.8 0.8 0.8 1.0"/>
  </material>
  <material name="orange">
    <color rgba="1.0 0.423529411765 0.0392156862745 1.0"/>
  </material>
  <material name="brown">
    <color rgba="0.870588235294 0.811764705882 0.764705882353 1.0"/>
  </material>
  <material name="red">
    <color rgba="0.80078125 0.12890625 0.1328125 1.0"/>
  </material>
  <material name="white">
    <color rgba="1.0 1.0 1.0 1.0"/>
  </material>


 <!-- Base -->
	<!-- <link name="dummy_link"/>

  <joint name="base_joint" type="fixed">
    <origin rpy="0 0 0" xyz="0 0 0"/>
		<child link="link_chassis"/>
    <parent link="dummy_link"/>
  </joint> -->

<!-- Unidades: Tiempo: 10*Segundo  -  Distancia: Decimetro  - Masa: 40*Kg -->

  <link name="link_chassis">
    <!-- pose and inertial -->
    <pose>0 0 0 0 0 0</pose>
    <inertial>
      <mass value="10.36"/>
      <origin rpy="0 0 0" xyz="1.5e-2 0 0.642"/>
      <inertia ixx="4.688" ixy="9.404e-5" ixz="1.335e-1" iyy="4.364" iyz="-1.6e-3" izz="9.11e-1"/>
    </inertial>
    <!-- body -->
    <collision name="collision_chassis">
      <origin rpy="0 0 0" xyz="0 0 0.2"/>
      <geometry>
        <box size="0.1 0.6 1.5"/>
        <!-- <mesh filename="package://simulation/stl/Body.stl" scale="10 10 10"/> -->
      </geometry>
    </collision>
    <visual>
      <origin rpy="0 0 0" xyz="0 0 0"/>
      <geometry>
        <!-- <box size="0.1 0.6 1.5"/> -->
        <mesh filename="package://simulation/stl/Body.stl" scale="10 10 10"/>
      </geometry>
      <material name="grey"/>
    </visual>
  </link>


<!-- IMU -->

<joint name="joint_IMU" type="fixed">
  <origin rpy="0 0 0" xyz="0 0 -0.328"/>
  <child link="link_IMU"/>
  <parent link="link_chassis"/>
</joint>

<link name="link_IMU">
  <!-- pose and inertial -->
  <pose>0 0 0 0 0 0</pose>
  <inertial>
    <mass value="0.2"/>
    <origin rpy="0 0 0" xyz="0 0 0"/>
    <inertia ixx="0.0004" ixy="0" ixz="0" iyy="0.0006" iyz="0" izz="0.001"/>
  </inertial>
  <!-- body -->
  <collision name="collision_chassis">
    <origin rpy="0 0 0" xyz="0 0 0"/>
    <geometry>
      <box size="0.21 0.16 0.02"/>
    </geometry>
  </collision>
</link>


<!--Gearbox and Wheels -->
<!-- Left -->

  <joint name="joint_left_gb" type="continuous">
    <origin rpy="0 0 0" xyz="0 0.316 -0.422"/>
    <child link="link_left_gb"/>
    <parent link="link_chassis"/>
    <axis rpy="0 0 0" xyz="0 1 0"/>
    <!-- <limit effort="0.8" velocity="30"/> -->
    <dynamics damping="0" friction="0"/>  <!-- Friction implemented in pybullet-->
  </joint>

  <link name="link_left_gb">
    <inertial>
      <mass value="0.56"/>
      <origin rpy="0 0 0" xyz="0 0 0"/>
      <inertia ixx="0.02544" ixy="0" ixz="0" iyy="0.04484" iyz="0" izz="0.02544"/>
    </inertial>
    <collision name="link_left_gb_collision">
      <origin rpy="0 1.5707 1.5707" xyz="0 0.05 0"/>
      <geometry>
        <cylinder length="0.1" radius="0.2"/>
      </geometry>
    </collision>
    <visual name="link_left_gb_visual">
      <origin rpy="0 1.5707 1.5707" xyz="0 0.05 0"/>
      <geometry>
        <cylinder length="0.1" radius="0.2"/>
      </geometry>
      <material name="green"/>
    </visual>
  </link>

  <joint name="joint_left_wheel" type="revolute">
    <limit lower="-0.03055" upper="0.03055" />
    <origin rpy="0 0 0" xyz="0 0 0"/>
    <child link="link_left_wheel"/>
    <parent link="link_left_gb"/>
    <axis rpy="0 0 0" xyz="0 1 0"/>
    <!-- <limit effort="0.8" velocity="30"/> -->
    <dynamics damping="0" friction="0"/>  <!-- Friction implemented in pybullet-->
  </joint>

  <link name="link_left_wheel">
    <inertial>
      <mass value="0.6"/>
      <origin rpy="0 0 0" xyz="0 0.142 0"/>
      <inertia ixx="0.02544" ixy="0" ixz="0" iyy="0.04484" iyz="0" izz="0.02544"/>
    </inertial>
    <collision name="link_left_wheel_collision">
      <origin rpy="0 1.5707 1.5707" xyz="0 0.125 0"/>
      <geometry>
        <cylinder length="0.25" radius="0.325"/>
        <!-- <mesh filename="package://simulation/stl/Wheel.stl" scale="10 10 10"/> -->
      </geometry>
    </collision>
    <visual name="link_left_wheel_visual">
      <origin rpy="3.14159 0 1.5707" xyz="0 0 0"/>
      <geometry>
        <!-- <cylinder length="0.005" radius="0.02"/> -->
        <mesh filename="package://simulation/stl/Wheel.stl" scale="10 10 10"/>
      </geometry>
      <material name="blue"/>
    </visual>
  </link>


<!-- Right -->

  <joint name="joint_right_gb" type="continuous">
    <origin rpy="0 0 0" xyz="0 -0.316 -0.422"/>
    <child link="link_right_gb"/>
    <parent link="link_chassis"/>
    <axis rpy="0 0 0" xyz="0 1 0"/>
    <!-- <limit effort="0.8" velocity="30"/> -->
    <dynamics damping="0" friction="0"/>  <!-- Friction implemented in pybullet-->
  </joint>

  <link name="link_right_gb">
    <inertial>
      <mass value="0.56"/>
      <origin rpy="0 0 0" xyz="0 0 0"/>
      <inertia ixx="0.02544" ixy="0" ixz="0" iyy="0.04484" iyz="0" izz="0.02544"/>
    </inertial>
    <collision name="link_right_gb_collision">
      <origin rpy="0 1.5707 1.5707" xyz="0 -0.05 0"/>
      <geometry>
        <cylinder length="0.1" radius="0.2"/>
      </geometry>
    </collision>
    <visual name="link_right_gb_visual">
      <origin rpy="0 1.5707 1.5707" xyz="0 -0.05 0"/>
      <geometry>
        <cylinder length="0.1" radius="0.2"/>
      </geometry>
      <material name="green"/>
    </visual>
  </link>

  <joint name="joint_right_wheel" type="revolute">
    <limit lower="-0.03055" upper="0.03055" />
    <origin rpy="0 0 0" xyz="0 0 0"/>
    <child link="link_right_wheel"/>
    <parent link="link_right_gb"/>
    <axis rpy="0 0 0" xyz="0 1 0"/>
		<!-- <limit effort="0.8" velocity="30"/> -->
    <dynamics damping="0" friction="0"/>  <!-- Friction implemented in pybullet-->
  </joint>

  <link name="link_right_wheel">
    <inertial>
      <mass value="0.6"/>
      <origin rpy="0 0 0" xyz="0 -0.142 0"/>
      <inertia ixx="0.02544" ixy="0" ixz="0" iyy="0.04484" iyz="0" izz="0.02544"/>
    </inertial>
    <collision name="link_right_wheel_collision">
      <origin rpy="0 1.5707 1.5707" xyz="0 -0.125 0"/>
      <geometry>
        <cylinder length="0.25" radius="0.325"/>
        <!-- <mesh filename="package://simulation/stl/Wheel.stl" scale="10 10 10"/> -->
      </geometry>
    </collision>
    <visual name="link_right_wheel_visual">
      <origin rpy="0 0 -1.5707" xyz="0 0 0"/>
      <geometry>
        <!-- <cylinder length="0.005" radius="0.02"/> -->
        <mesh filename="package://simulation/stl/Wheel.stl" scale="10 10 10"/>
      </geometry>
      <material name="blue"/>
    </visual>
  </link>

</robot>

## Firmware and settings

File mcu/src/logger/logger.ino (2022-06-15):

/*
  ============================================
  Balancio-Kit is placed under the MIT License
  Copyright (c) 2021 by Linar (UdeSA)

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
  THE SOFTWARE IS PROVIDED "AS IS", WITHOUT WARRANTY OF ANY KIND, EXPRESS OR
  IMPLIED, INCLUDING BUT NOT LIMITED TO THE WARRANTIES OF MERCHANTABILITY,
  FITNESS FOR A PARTICULAR PURPOSE AND NONINFRINGEMENT. IN NO EVENT SHALL THE
  AUTHORS OR COPYRIGHT HOLDERS BE LIABLE FOR ANY CLAIM, DAMAGES OR OTHER
  LIABILITY, WHETHER IN AN ACTION OF CONTRACT, TORT OR OTHERWISE, ARISING FROM,
  OUT OF OR IN CONNECTION WITH THE SOFTWARE OR THE USE OR OTHER DEALINGS IN
  THE SOFTWARE.
  ===============================================
*/

#include "config.h"
#include "dc_motor.h"
#include "controllers.h"
#include "imu.h"
#include "timer.h"
#include "Wire.h"
#include "commander.h"
#include <WiFi.h>

const char* ssid = "*****";           // Complete with your network SSID (name)!
const char* password = "*****";       // Complete with your network password!
const uint16_t port = 8090;
const char * host = "192.168.10.108"; // Complete with your host's IP!
WiFiClient client;

float current_angle_data [1000];
float target_angle_data [1000];
float pwm_data [1000];
int iteration_counter = 0;

float currentAngle = 0.0, targetAngle = STATIC_ANGLE, angle_limit = 0.5;
float yaw = 0.0, targetYaw = 0.0, yawCommand = 0.0;
int pwmL = 0, pwmR = 0;
volatile bool controlFlag = false;
float fwd = 0;
float rot = 0;
int time_ctr = 0, time_ctr2 = 0;
bool stop_command = false;
bool x_down;

String control_algo(CONTROL_ALGO);
controller_data_t pitch_controller_data = {KP, KI, KD};
controller_data_t yaw_controller_data = {KP_YAW, KI_YAW, KD_YAW};

Controller *yaw_control;
Controller *pitch_control;
std::vector<float> pwm;
std::vector<float> rot_v;

void setup()
{
    // UART PC connection
    Serial.begin(115200);

    // Motor initialization
    motor_init();

    // IMU init
    imu_setup();

    // Bluetooth init
    ps3_setup();

    // Timer init. (ISR at 1/LOOP_PERIOD Hz)
    timer_init();

    // Controllers init
    pitch_control = Controller::init_algo("PID", pitch_controller_data);
    yaw_control = Controller::init_algo("PID", yaw_controller_data);

    // Wifi init
    WiFi.begin(ssid, password);
    while (WiFi.status() != WL_CONNECTED) {
        delay(500);
        Serial.println("...");
    }

    Serial.print(F("WiFi connected with IP: "));
    Serial.println(WiFi.localIP());
    while (!client.connect(host, port)) {

        Serial.println(F( "Connection to host failed" ));

        delay(1000);
    }

    Serial.println(F( "Connected to server" ));
}

// ISR at 1/LOOP_PERIOD Hz
void IRAM_ATTR onTime()
{
    controlFlag = true;
}

void loop()
{
    while (iteration_counter < 600) 
    {

        if (controlFlag)
        {
            if (iteration_counter > 400)
            {
                targetAngle = 0.04;
            }

            // Get pitch and yaw angles.
            currentAngle = updatePitch(currentAngle);
            yaw = updateYaw(yaw);

            if (control_algo.equals("PID"))
            {
                // PID control.
                pwm = pitch_control->update(currentAngle, targetAngle);
                pwmL = pwm.at(0);
                pwmR = pwm.at(0);
            }
            else if (control_algo.equals("RL"))
            {
                // RL control.
                pwm = pitch_control->update(currentAngle, targetAngle);
                pwmL = pwm.at(0);
                pwmR = pwm.at(1);
            }

            // Yaw control.
            rot_v = yaw_control->update(yaw, targetYaw);
            rot = 0;  //rot_v.at(0);

            // Pass PWM commands to motors.
            L_motor(pwmL + int(rot)); // -255 to 255
            R_motor(pwmR - int(rot)); // -255 to 255

            // Print relevant data.
            if (true)
            {
                // Serial.print(F( "  targetAngle: " ));
                // Serial.print(targetAngle);
                // Serial.print(F( "  targetYaw: " ));
                // Serial.print(targetYaw);
                // Serial.print(F( " pitch: " ));
                // Serial.print(currentAngle);
                // Serial.print(F( "  PWM: " ));
                // Serial.print(pwmL);
                // Serial.print(F( " Loop time: " ));
                // Serial.println(micros() - time_ctr);
                // time_ctr = micros();

                // Logger
                current_angle_data[iteration_counter] = currentAngle;
                target_angle_data[iteration_counter] = targetAngle;
                pwm_data[iteration_counter] = pwmL;
                iteration_counter++;
            }
            controlFlag = false;
        }
        else
        {
            return;
        }
    }

    // Stop motors
    stop_motor();

    // Send data to server.
    // Send current angle data.
    client.print("|");
    for (int i = 0; i < iteration_counter; i++)
    {
        client.print(",");
        client.print(current_angle_data[i]);
        delay(1);
    }

    // Send target angle data.
    client.print("|");
    for (int i = 0; i < iteration_counter; i++)
    {
        client.print(",");
        client.print(target_angle_data[i]);
        delay(1);
    }

    // Send PWM data.
    client.print("|");
    for (int i = 0; i < iteration_counter; i++)
    {
        client.print(",");
        client.print(pwm_data[i]);
        delay(1);
    }


    client.stop();

    while(true){
    }
}

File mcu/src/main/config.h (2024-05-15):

/*
======================================================================
 Balancio-Kit (c) 2021 Linar (UdeSA)
 This code is licensed under MIT license (see LICENSE.txt for details)
======================================================================
*/
#pragma once
// Control algorithm type
#define CONTROL_ALGO "PID" // PID, RL, ...
#include <string>

String CONTROLLER_DEVICE = "APP"; //"APP , PS3, ..."
// Reinforcement Learning model name. Available models are located in the folder named "models".
#define A2C_p_1

// PID Constants for pitch control
#define KP 2000  // 2000     //1200    //1750
#define KI 22000 // 22000     //22000   //11000
#define KD 20.0  // 20.0     //17.0    //25.0

// P constant for yaw cotrol
#define KP_YAW 5.0
#define KI_YAW 0.0
#define KD_YAW 0.05

// RL parameters
#define NUMBER_OF_INPUTS 1
#define NUMBER_OF_OUTPUTS 2
#define RL_INPUT_NORMALIZATION 1.5708   // (in_norm = in / RL_INPUT_NORMALIZATION)   --- //1.5708  // 0.06519447
#define RL_OUTPUT_DENORMALIZATION 255.0 // (out = out_norm * RL_OUTPUT_DENORMALIZATION)
#define TENSOR_ARENA_SIZE 16 * 1024     // You may need to tweak this value.

// Loop period in seconds
#define LOOP_PERIOD 0.01 // 100 Hz

#define STATIC_ANGLE -0.04 // Calibrated point

// IMU calibration parameters
#define X_ACCEL_OFFSET -1775
#define Y_ACCEL_OFFSET 756
#define Z_ACCEL_OFFSET 2706
#define X_GYRO_OFFSET 181
#define Y_GYRO_OFFSET 77
#define Z_GYRO_OFFSET 60

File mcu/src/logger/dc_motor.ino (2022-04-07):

/* 
======================================================================
 Balancio-Kit (c) 2021 Linar (UdeSA)
 This code is licensed under MIT license (see LICENSE.txt for details)
====================================================================== 
*/

#include "dc_motor.h"

#define L_CHANNEL 0
#define R_CHANNEL 1

int PWM_freq = 200;

void motor_init(void)
{
  // Pins configuration
  pinMode(IN1, OUTPUT);
  pinMode(IN2, OUTPUT);
  pinMode(IN3, OUTPUT);
  pinMode(IN4, OUTPUT);

  // Start with stopped motor
  stop_motor();

  // PWM
  ledcAttachPin(ENA, L_CHANNEL);     // (Pin, Channel)
  ledcAttachPin(ENB, R_CHANNEL);     // (Pin, Channel)
  ledcSetup(L_CHANNEL, PWM_freq, 8); // (Channel, PWM frequency, bits resolution)
  ledcSetup(R_CHANNEL, PWM_freq, 8); // (Channel, PWM frequency, bits resolution)
  ledcWrite(L_CHANNEL, 0);           // (channel, bits)
  ledcWrite(R_CHANNEL, 0);           // (channel, bits)
}

void stop_motor(void)
{
  digitalWrite(IN1, LOW);
  digitalWrite(IN2, LOW);
  digitalWrite(IN3, LOW);
  digitalWrite(IN4, LOW);
}

void bwd_L_motor(int pwm)
{
  // PWM 8 bits int --> [0; 255]
  digitalWrite(IN1, HIGH);
  digitalWrite(IN2, LOW);
  ledcWrite(L_CHANNEL, pwm);
}

void bwd_R_motor(int pwm)
{
  // PWM 8 bits int --> [0; 255]
  digitalWrite(IN3, LOW);
  digitalWrite(IN4, HIGH);
  ledcWrite(R_CHANNEL, pwm);
}

void fwd_L_motor(int pwm)
{
  // PWM 8 bits int --> [0; 255].
  digitalWrite(IN1, LOW);
  digitalWrite(IN2, HIGH);
  ledcWrite(L_CHANNEL, pwm);
}

void fwd_R_motor(int pwm)
{
  // PWM 8 bits int --> [0; 255].
  digitalWrite(IN3, HIGH);
  digitalWrite(IN4, LOW);
  ledcWrite(R_CHANNEL, pwm);
}

void R_motor(int pwm)
{
  pwm = constrain(pwm, -255.0, 255.0);
  if (pwm >= 0)
  {
    fwd_R_motor(pwm);
  }
  else
  {
    bwd_R_motor(-pwm);
  }
}

void L_motor(int pwm)
{
  pwm = constrain(pwm, -255.0, 255.0);
  if (pwm >= 0)
  {
    fwd_L_motor(pwm);
  }
  else
  {
    bwd_L_motor(-pwm);
  }
}

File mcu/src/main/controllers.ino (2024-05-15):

/* 
======================================================================
 Balancio-Kit (c) 2021 Linar (UdeSA)
 This code is licensed under MIT license (see LICENSE.txt for details)
====================================================================== 
*/

#include "config.h"
#include "controllers.h"
#include "rl_model.h"
#include <EloquentTinyML.h>
#include <vector>
#include "Arduino.h"

/* Controller Abstract Class*/

Controller *Controller::init_algo(String algo, controller_data_t controller_data)
{
    // Control algorithm initialization
    if (algo.equals("PID"))
    {
        // PID
        return new PID(controller_data.kp, controller_data.ki, controller_data.kd, 5.0);
    }
    else if (algo.equals("RL"))
    {
        // RL
        return new RlSingleInput();
    }
    else
    {
        Serial.println("Error loading control algorithm");
    }
}

/*RL Single Input Class*/

RlSingleInput::RlSingleInput(void)
{
    /* Neural Network */
    ml = Eloquent::TinyML::TfLite<NUMBER_OF_INPUTS, NUMBER_OF_OUTPUTS, TENSOR_ARENA_SIZE>();
    ml.begin(rl_model);
}

std::vector<float> RlSingleInput::update(float current_state, float target_state)
{
    std::vector<float> output;

    // Input Normalization (for neural net compatibility).
    // WARNING: This must be the same normalization used during training.
    error = current_state - target_state;
    error /= RL_INPUT_NORMALIZATION;
    error = constrain(error, -1, 1);

    float input[1] = {error};
    float predicted[2] = {0};
    ml.predict(input, predicted);

    output.push_back(RL_OUTPUT_DENORMALIZATION * predicted[0]);
    output.push_back(RL_OUTPUT_DENORMALIZATION * predicted[1]);

    return output;
}

/*PID Class*/

PID::PID(float kp_init, float ki_init, float kd_init, float sum_constraint_init)
{
    kp = kp_init;
    ki = ki_init;
    kd = kd_init;
    sum_constraint = sum_constraint_init; 
}

std::vector<float> PID::update(float current_state, float target_state)
{
    std::vector<float> output;

    error = current_state - target_state;
    errorSum += error;
    errorSum = constrain(errorSum, -sum_constraint, sum_constraint);
    out = kp * (error) + ki * (errorSum)*LOOP_PERIOD + kd * (current_state - prev_state) / LOOP_PERIOD;
    prev_state = current_state;

    output.push_back(out);
    return output;
}

void PID::reset(float previous_state)
{
    errorSum = 0.0;
    prev_state = previous_state;
}

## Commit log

2021-06-23 Updated motor PWM channels
2021-06-23 PID tunning
2021-06-24 Implemented motor model and Karnopp friction model.
2021-06-24 Daily changes.
    [balancio_v0.urdf]
2021-06-24 Added gear joint in URDF for backlash compatibility.
    [balancio_v1.urdf, balancio_v1_backlash_debug.urdf]
2021-06-24 Added backlash simulation in dc motors.
    [motor.py]
2021-06-30 Modified static friction implementation. It now considers external torques.
2021-07-01 Removed friction overlapping in URDF.
    [balancio_v1.urdf]
2021-07-02 Added Normalization and Backlash flags to environments.
2021-07-30 New URDF with real masses and inertia.
    [balancio_v2.urdf]
2021-07-30 New URDF with real masses and inertia (Scaled).
    [balancio_v3.urdf]
2021-07-30 Changed actual backlash
    [balancio_v1_backlash_debug.urdf]
2021-07-30 Changed bullet units and added RL/PID mode functionality.
2021-07-30 Rescaled motor constants.
2021-07-30 Balancio V0.4 STL files.
    [Body.stl, Wheel.stl]
2021-07-30 Changed imu processing and calibration values for Balancio V0.4.
2021-07-30 Renamed pid tester file
2021-08-06 Added robot methods to get observations (pitch, yaw, acceleration, angular velocity)
2021-08-07 Extended gym environment (primarily the state observations). Added flags for easy options selection. Added imu simulation (complementary filter). Added buffer ( w/ variable length) for observation me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
2021-08-07 Adapted PID script, with new gym environment.
2021-09-10 Added live data plot and fixed complementary filter.
2021-09-17 Changed (simplified) wheel collision shape.
    [balancio_v3.urdf]
2021-09-17 Added stiffness and damping to wheel-floor contact. This improves the acceleration measurement, as reduces noise. Also fixed inertia bug. Now the inertia tensor is being loaded from the URDF.
2021-09-18 Added IMU link, for real-sim compatibility.
    [balancio_v3.urdf]
2021-09-18 Added IMU link, for real-sim compatibility. Added wheels friction, which improves sim stability.
2021-12-22 Code rearrangement.
    [Body.stl, Wheel.stl, balancio_v0.urdf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]
2022-03-08 Added gyro in z (gravity) direction
2022-03-08 Added yaw controller. Added angle limit to stop motors. Changed ps3 controller mac adress
2022-03-23 Code refactor.
    Added config.h file, to store constant configuration variables. Changed
    control (PID) code arquitecture.
2022-03-23 Tuned Yaw PD controller.
2022-03-31 Add functionality to stop motors via joystick.
2022-04-01 Reset PID when robot is stopped.
    [config.h, controllers.ino, main.ino]
2022-04-07 Simplify IMU driver.
2022-04-08 Rename controller variables. Replace 'angle' with 'state'.
    [controllers.ino]
2022-04-25 Add missing type hintings.
    [motor.py]
2022-05-05 Change sampler network variable, to optimize code. Remove saving in pickle format.
2022-05-05 Add good policy, using only pitch as input.
2022-05-05 Make case-insensitive checks.
2022-05-06 Add robot method to obtain linear velocity in the imu coordinates.
2022-05-06 Remove old TODO.
    [balancio_v2.urdf]
2022-06-14 Create Planos de Impresión
2022-06-15 Add logger. Arduino sketch and python script to send and save data.
2022-06-21 Change pwm pin to avoid wheel rotation at startup.
2023-10-03 Debería estar terminado. HAbria que probarlo devuelta para estar seguros
2023-10-03 Update valores PID
2024-05-15 Fix motorreductor explanation
2024-07-17 Update esp32 lib version.md
